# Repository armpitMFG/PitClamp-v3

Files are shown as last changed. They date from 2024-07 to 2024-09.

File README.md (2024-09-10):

# Note: This project is obsolete. Use [PitClamp Mini](https://github.com/armpitMFG/PitClamp-Mini) instead

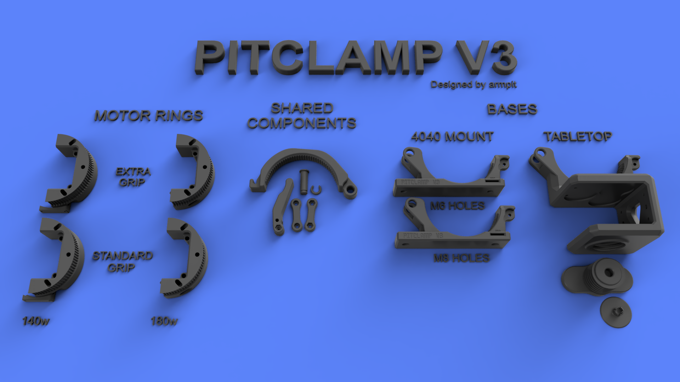
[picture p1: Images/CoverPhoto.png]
PitClamp v3 README Cover Photo


# PitClamp v3 Quick Release Nema23 Mount 
**Summary**  
Highly secure mounting and easy rotational adjustment of iHSV57 and 57AIM Nema23 motor  
Substantially stronger & grippier than previous PitClamp versions  
4 degree rotational granularity  
Supports sensor-homing cable passthrough  
Motor can be completely removed for storage  
Selection of bases for different use cases  

**Motor compatibility**  
- 180w JMC iHSV57 with v2 reference board  
  - Full 360 degree range of movement
- 140w JMC iHSV57 with v2 reference board
  - 80 degree (-40 to 40 from horizontal)
- 140w JMC iHSV57 with relocated (or future) reference board
  - Full 360 degree
- 100w JMC iHSV57 with v2 reference board
  - Not supported
- 100w JMC iHSV57 with relocated (or future) reference board
  - 200 degree (-100 to 100 from horizontal) 
- "Gold motor" 57AIM30C with relocated (or future) reference board
  - Full 360 degree

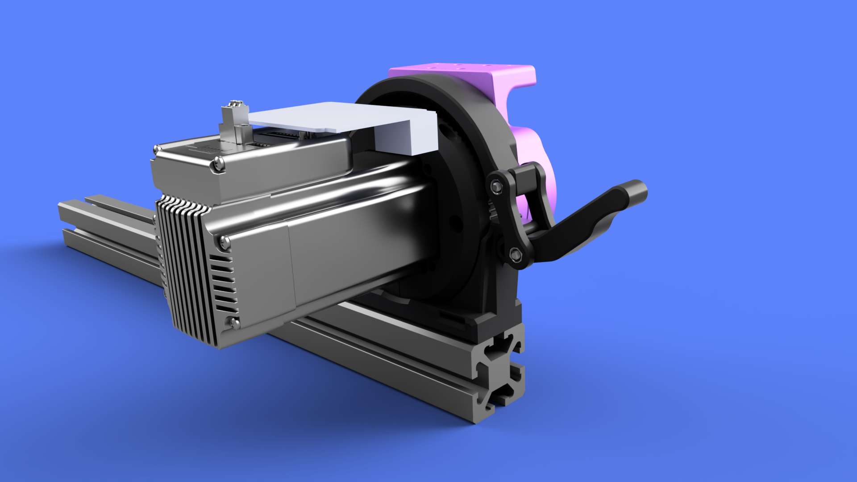
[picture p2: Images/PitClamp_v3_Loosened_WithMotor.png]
PitClamp v3 README Cover Photo2
  

## [PitClamp v3 - Motor Rings](Files/Motor%20Rings)
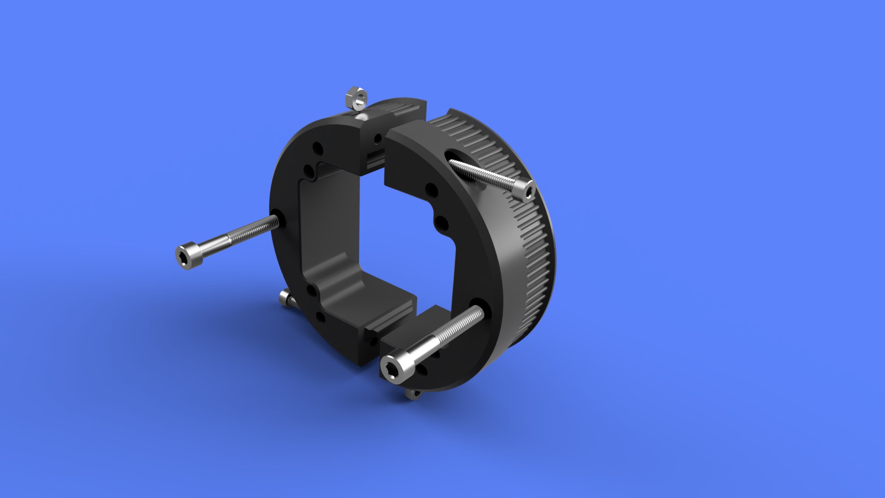
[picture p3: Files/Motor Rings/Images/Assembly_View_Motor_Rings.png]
Motor Rings Assembly View
  

**Summary**  
Motor rings for attaching iHSV57 and 57AIM Nema23 motors to PitClamp v3 mounts  

**File variations**  
- EXTRAGRIP
  - Clunkier adjustment, but provides extra grip strength
  - Not recommended unless you have grip issues with the standard
- 140w
  - Supports 140w motors with v2 reference board mounting support
  - Pair one of these with a standard half if you use 140w

**Part list**  
- Motor Ring Half
- Motor Ring Half EXTRAGRIP
- Motor Ring Half 140w
- Motor Ring Half EXTRAGRIP 140w

**Hardware**  
- 2x M4x16 (M4x25 max) Socket Cap Head Bolt (w/ Optional 2x M4 Nut for added strength, likely unnecessary)
- 2x M5x35 (M5x50 max) Socket Cap Head Bolt (To attach to OSSM body)

**Printing**  
3 walls 20% infill  
No supports necessary  
(Must print with 0.2mm layer height for built-in support assists to work)  
If using 180w motor rings, print your selected ring twice; If using 140, replace one ring with the corresponding 140w variant  

**Assembly**  
(Optional, likely unnecessary) Insert M4 nut into each motor half slot  
Slide ring halves over motor and connect using M4x16 (M4x25 max) Socket Cap Head Bolt  
Connect motor ring assembly to OSSM Base using 2x M5x35 Socket Cap Head Bolts  

## [PitClamp v3 - Shared Components](Files/Shared%20Components/)
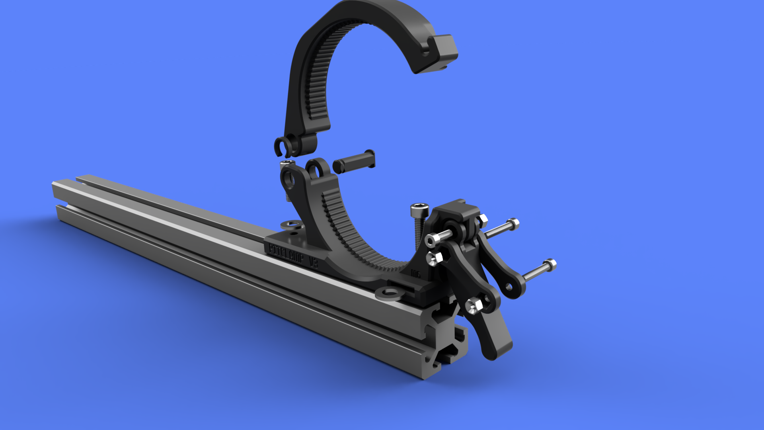
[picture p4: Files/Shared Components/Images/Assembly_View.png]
PitClamp v3 - Shared Components
  

**Summary**  
Components shared among all PitClamp v3 mounting bases

**Part list**
- Ring Upper
- Hinge Pin
- Hinge Pin Clip
- Handle
- Dogbone (Nut inset)
- Dogbone (Bolt inset)

**Hardware**  
- 2x M4x25 Socket Cap Head Bolt
- 1x M4x12 Socket Cap Head Bolt
- 3x M4 Nut

**Printing**  
3 walls 30% infill  
(Must print with 0.2mm layer height for built-in support assists to work)  
Supports required for Handle  

**Assembly**  
Insert M4 nuts into the Dogbone and Handle  
Attach Handle to the Ring Base using M4x12 Socket Cap Head Bolt (Hand tighten until snug, then back off 1/4 turn)  
Attach Dogbones to the Handle using M4x25 Socket Cap Head Bolt (Hand tighten until snug, then back off 1/4 turn)  

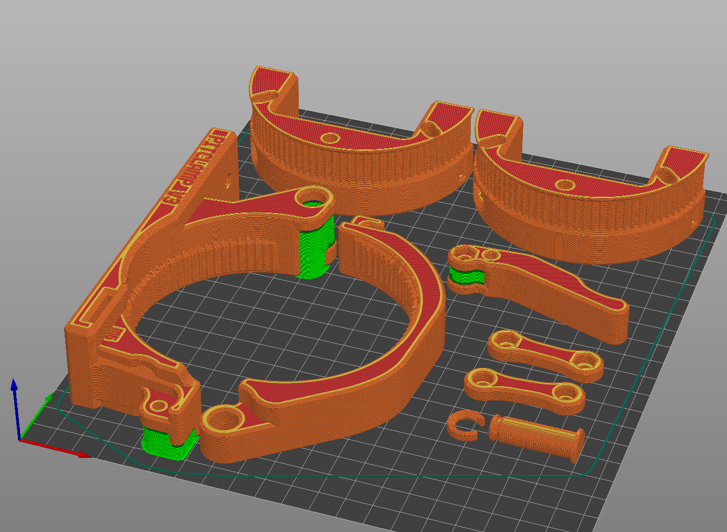
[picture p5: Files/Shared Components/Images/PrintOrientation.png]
PitClamp v3 - Shared Components
  

## [PitClamp v3 - 4040 Base](Files/Bases/40-4040)
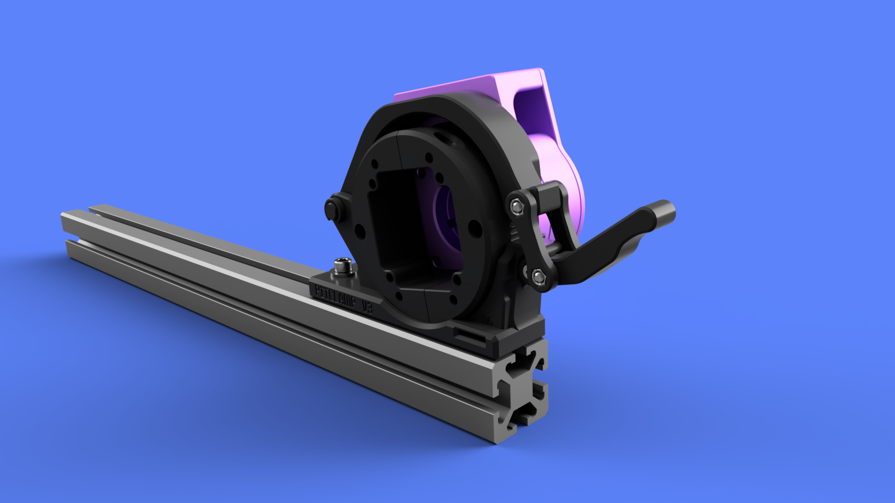
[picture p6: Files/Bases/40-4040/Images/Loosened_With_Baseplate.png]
PitClamp v3 - 4040 Base
  
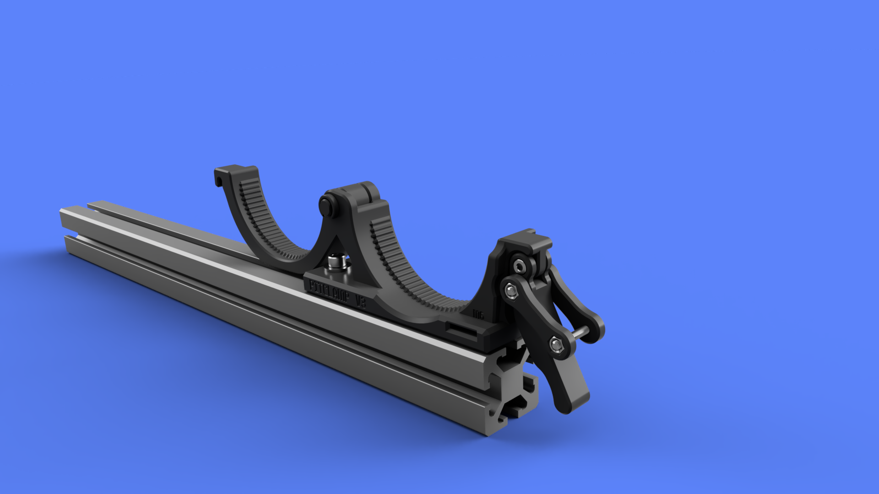
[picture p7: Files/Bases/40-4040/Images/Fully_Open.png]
PitClamp v3 - 4040 Base
  

**Summary**  
Base for attaching PitClamp v3 to 4040 aluminum extrusion  
60mm height when in 'storage' mode  

**File variations**  
- Ring Base M6 mounting hardware
- Ring Base M8 mounting hardware
  
**Hardware**  
- 2x M6x20 Socket Cap Head Bolt
- 2x ~12mm diameter M6 Washer (16mm max diameter, 2.4mm max thickness)
- 2x M6 T-Nut

**Printing**  
3 walls 30% infill  
(Must print with 0.2mm layer height for built-in support assists to work)  
Minimal supports around the hinge and handle attachment points  

**Assembly**  
Use M6x20 Socket Cap Head Bolt (or M8 on M8 version) and T-Nut to attach to 4040, washer for front slides into slot  
Attach Ring Upper to Ring Base using Hinge Pin and affix Hinge Pin Clip  

PitClamp v3 - 4040 Base Print Orientation  

## [PitClamp v3 - Tabletop Base](Files/Bases/Tabletop/)  

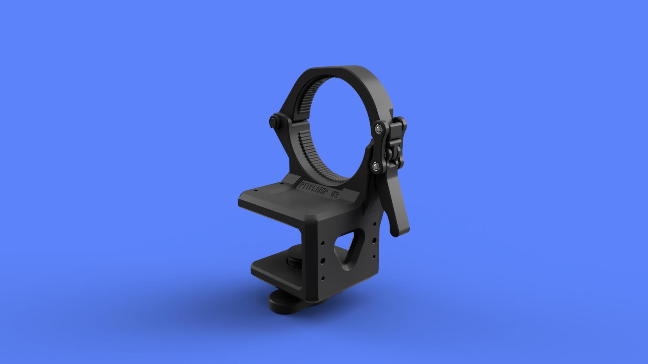
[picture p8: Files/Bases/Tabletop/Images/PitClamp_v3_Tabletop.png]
PitClamp v3 - Tabletop Base
  

**Summary**  
Allows for clamping to a tabletop, door or similar, ranging from 30mm-50mm  
For use with stroker attachments or for light-duty insertable use when attached to an interior door  

**Hardware**  
38mm furniture non-slip pads. Inexpensive, ~$3USD local or Amazon for 8pc.  
https://www.scotchbrand.com/3M/en_CA/p/d/v000277260/  

**Printing**  
3 walls, 30% infill minimum; More walls for stiffer clamp  
(Must print with 0.2mm layer height for built-in support assists to work)  
Minimal supports around the hinge and handle attachment points, but for cleaner threads you can use support there, too  
I chose not to support threads and worked fine on Ender3 v1 w/ PETG  
The screw and screw topper do not need support  

**Assembly**  
(Optional, but highly recommended) Attach 3 furniture gripping pads to the underside of the Tabletop Mount and 1 gripping pad to Screw Topper.  
Thread Screw through the Tabletop Mount and then snap Screw Topper into place

**Addons**  
M4,M6,M4 holes with 15mm spacing on center to support addons  
Currently no add-ons have been created  

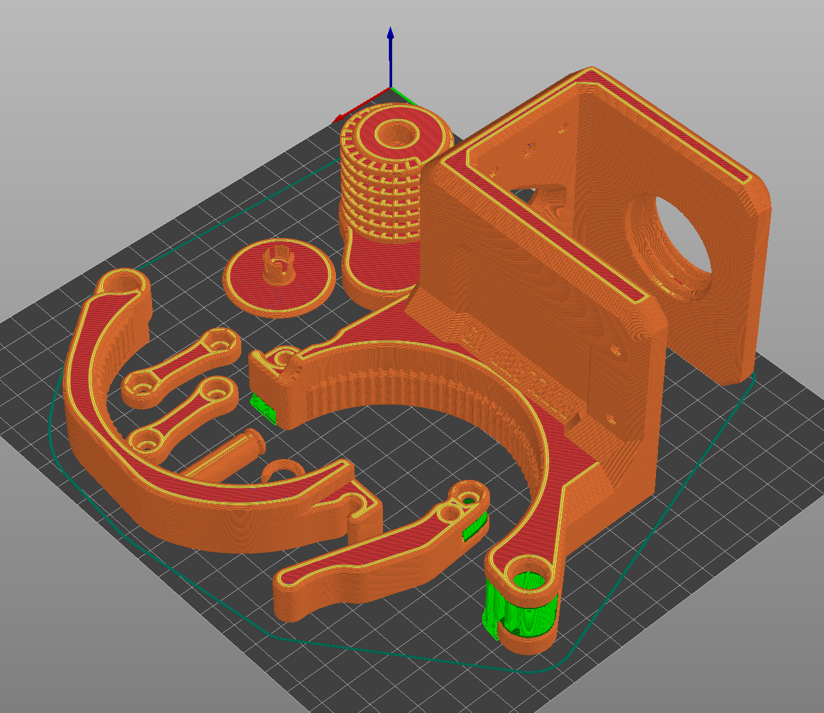
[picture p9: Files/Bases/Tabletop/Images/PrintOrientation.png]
PitClamp v3 - Tabletop Base Print Orientation


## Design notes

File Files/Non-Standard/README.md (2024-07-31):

These are non-standard parts that may be better for certain setups  

## Official non-standard parts:  
  
### /Handles/Handle_Forward
Remix author: armpit  
Default handle with an 80 degree bend to allow for PitClamp v3 use in setups where the handle cannot extend down past the PitClamp Base  

## 3rd party non-standard parts:  

### /20-4040/PitClamp_v3_Ring_Base_M5
Remix author: Macarize  
Default PitClamp v3 Base - 4040, but for 20-4040 extrusion and M5 holes  
  
### /dbiesn Head/PitClamp_v3_Motor_Ring_Half_EXTRAGRIP_dbiesn_head
Remix author: Jack   
Default Motor Ring Half EXTRAGRIP version for use with the dbiesn head

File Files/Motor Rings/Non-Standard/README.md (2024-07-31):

Same as normal ring, but the grooves are rotated 2 degrees which will point the device directly horizonal.

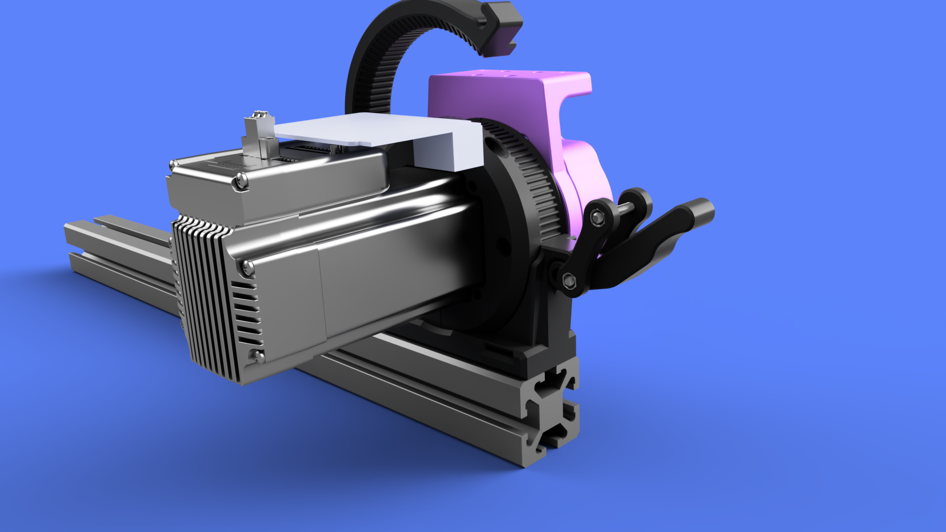
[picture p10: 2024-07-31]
Images/PitClamp_v3_Opened_WithMotor.png

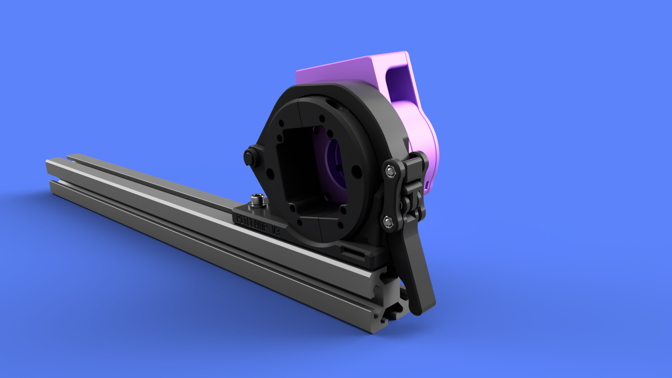
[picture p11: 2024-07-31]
Files/Bases/40-4040/Images/Clamped_With_Baseplate.png

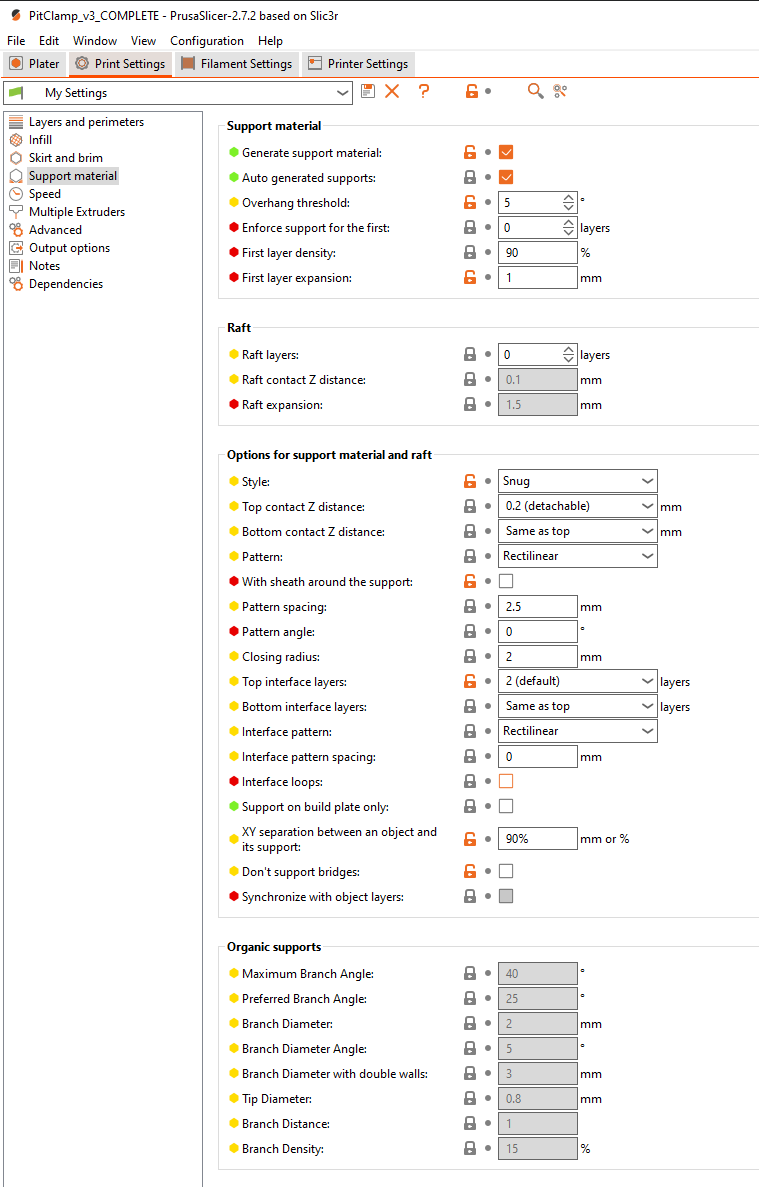
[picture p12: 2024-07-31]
Files/Bases/Tabletop/Images/SupportSettings.png

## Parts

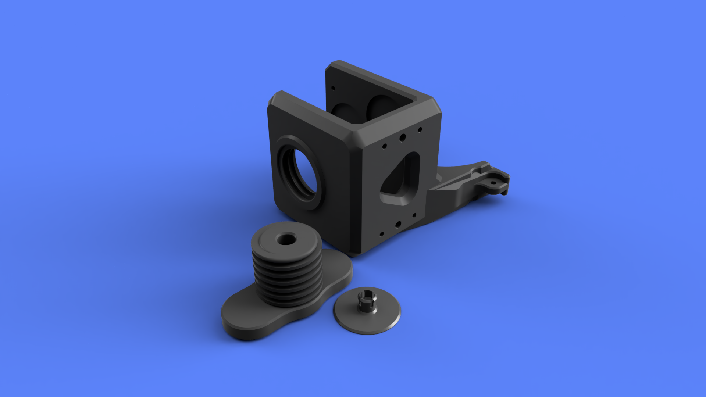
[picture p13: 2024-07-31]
Files/Bases/Tabletop/Images/PitClamp_v3_Tabletop_Parts.png

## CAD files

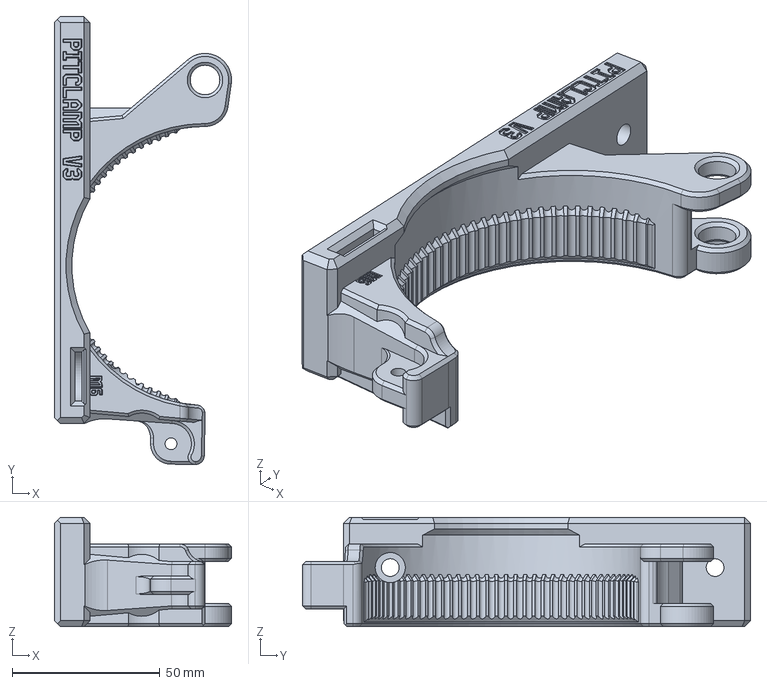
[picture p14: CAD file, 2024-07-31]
Files/Bases/40-4040/STEP/PitClamp_v3_Ring_Base_M6.step
60.0 x 151.7 x 37.0 mm

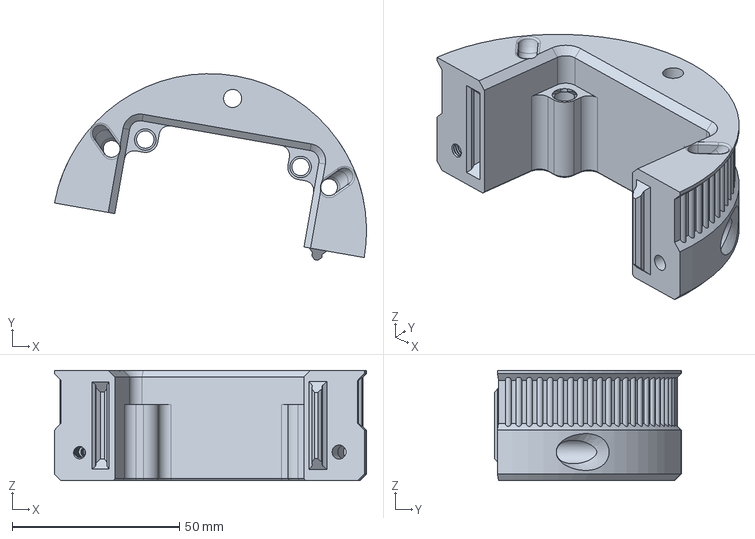
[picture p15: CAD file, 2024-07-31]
Files/Motor Rings/Non-Standard/PitClamp_v3_Motor_Ring_Half_HorizontalCompat.step
93.2 x 55.8 x 33.0 mm

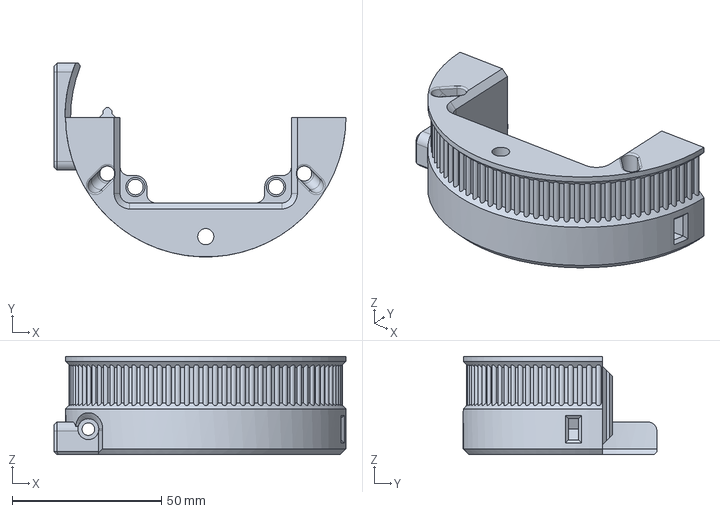
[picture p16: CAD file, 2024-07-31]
Files/Motor Rings/STEP/PitClamp_v3_Motor_Ring_Half_iHSV57-140w.step
97.9 x 64.9 x 33.0 mm

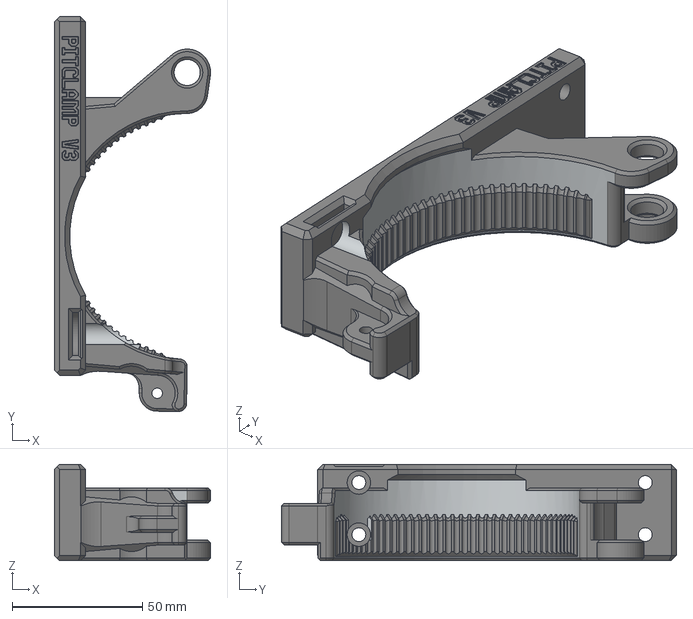
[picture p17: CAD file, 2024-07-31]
Files/Non-Standard/20-4040/STEP/PitClamp_v3_Ring_Base_M5.stp
60.0 x 151.7 x 37.0 mm

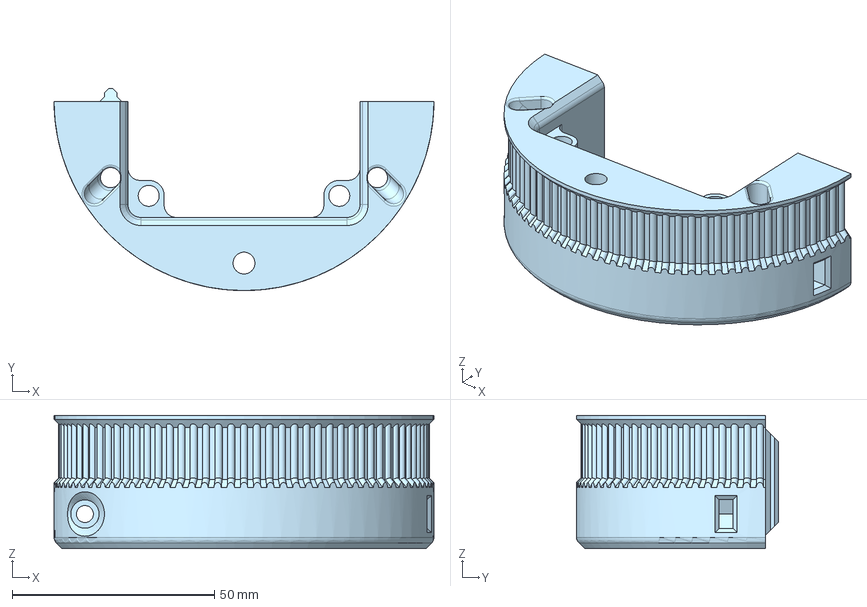
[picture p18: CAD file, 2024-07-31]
Files/Non-Standard/dbiesn Head/STEP/PitClamp_v3_Motor_Ring_Half_EXTRAGRIP_dbiesn_head.step
94.0 x 50.0 x 33.0 mm

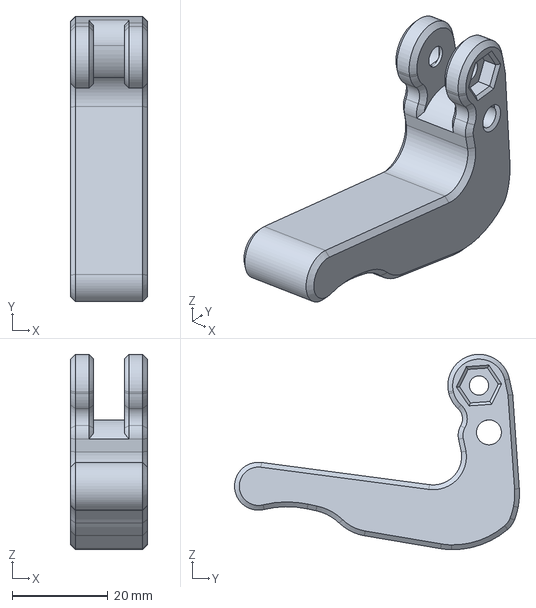
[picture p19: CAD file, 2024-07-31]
Files/Non-Standard/Handles/STEP/PitClamp_v3_Handle_Forward.step
16.0 x 59.5 x 40.8 mm

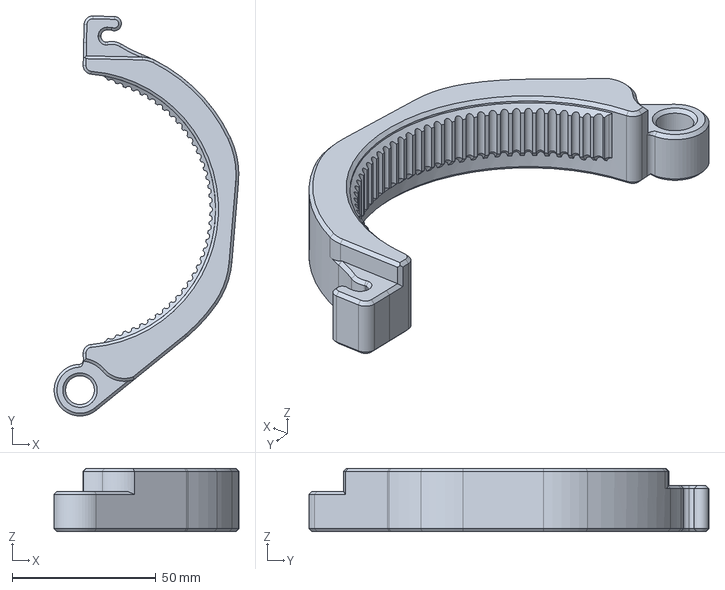
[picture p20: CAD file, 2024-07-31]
Files/Shared Components/STEP/PitClamp_v3_Ring_Upper.step
64.3 x 139.2 x 22.0 mm

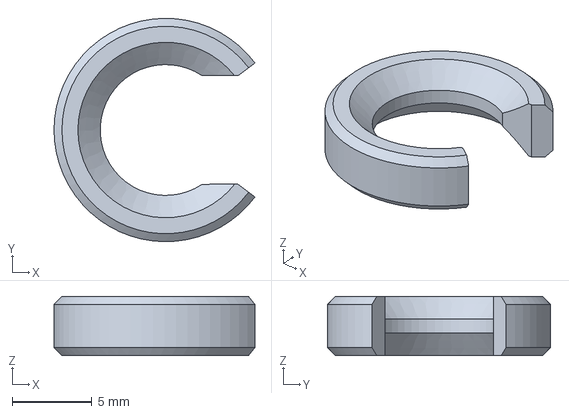
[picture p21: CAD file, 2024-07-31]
Files/Shared Components/STEP/PitClamp_v3_Hinge_Pin_Clip.step
12.6 x 14.0 x 3.70 mm

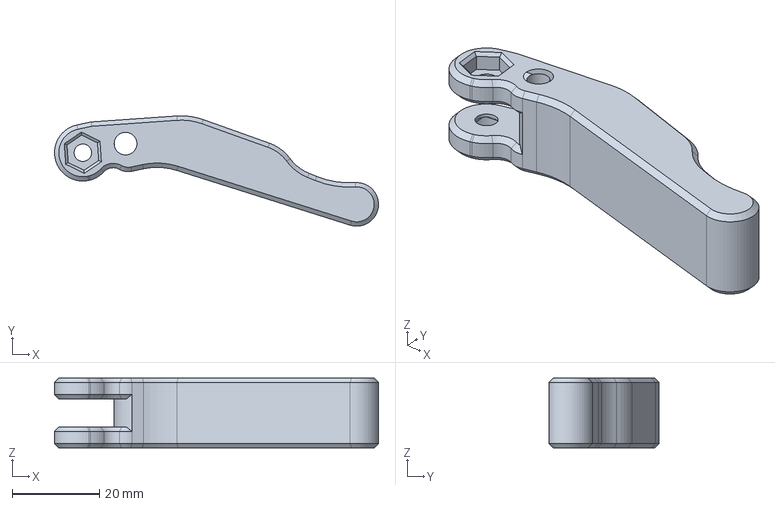
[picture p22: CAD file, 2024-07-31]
Files/Shared Components/STEP/PitClamp_v3_Handle.step
74.2 x 25.3 x 16.0 mm

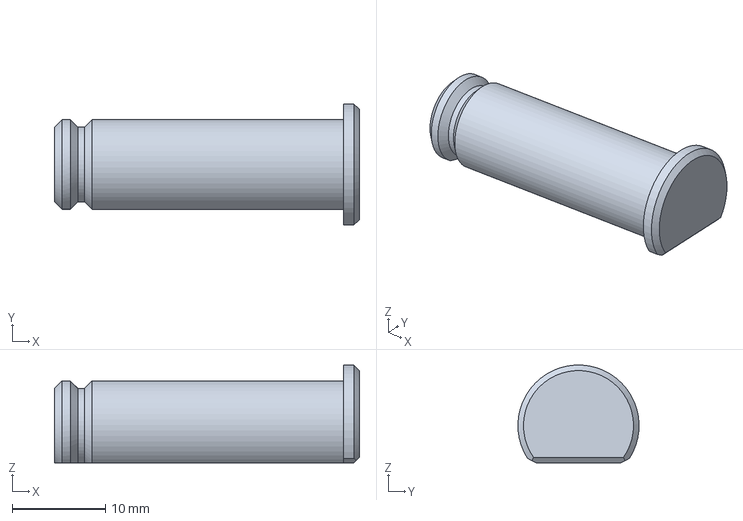
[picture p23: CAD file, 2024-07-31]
Files/Shared Components/STEP/PitClamp_v3_Hinge_Pin.step
32.7 x 13.0 x 10.5 mm

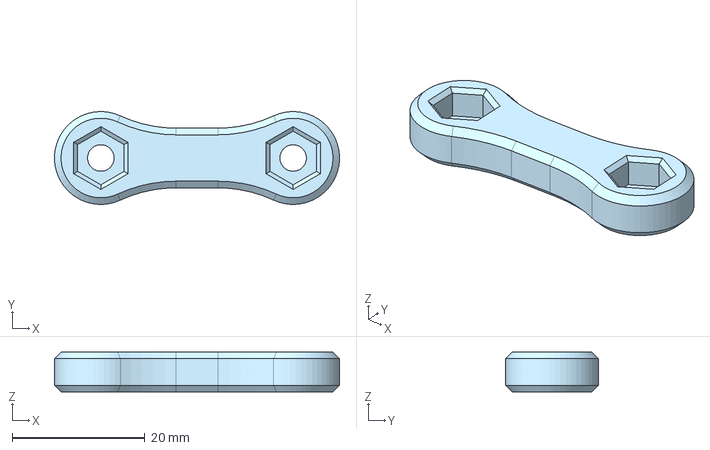
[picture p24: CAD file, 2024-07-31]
Files/Shared Components/STEP/PitClamp_v3_Dogbone_Nuts.step
43.0 x 14.0 x 6.00 mm

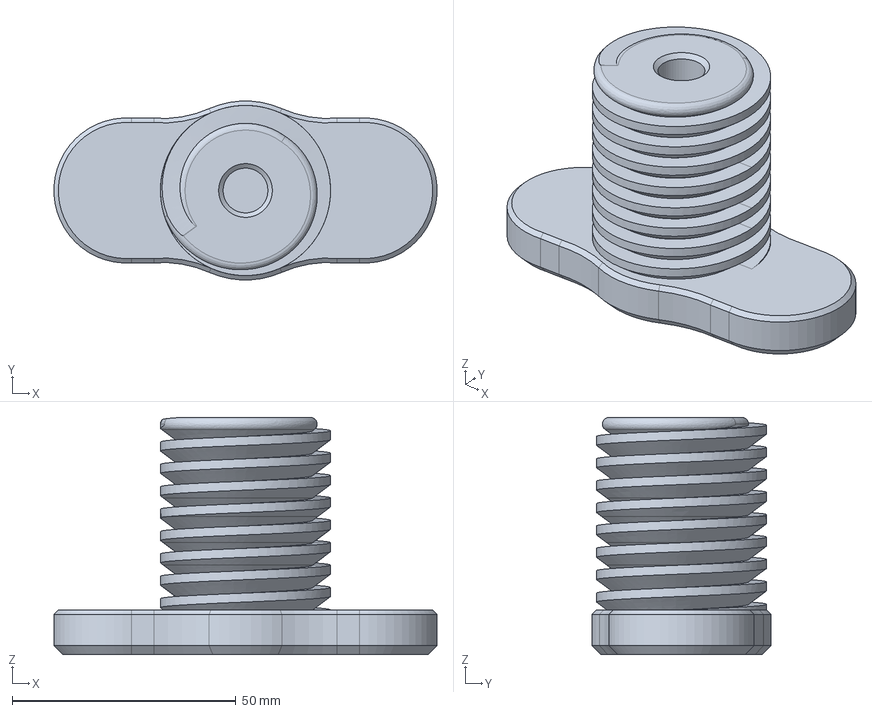
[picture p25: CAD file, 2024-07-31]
Files/Bases/Tabletop/STEP/PitClamp_v3_Tabletop_Screw+10mm.step
85.5 x 39.9 x 53.0 mm

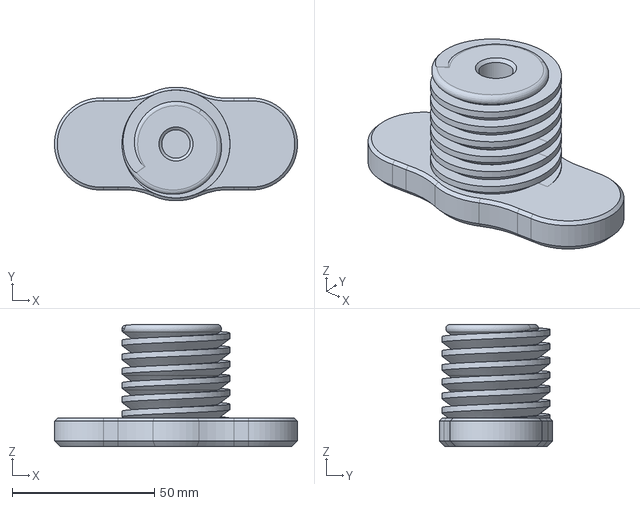
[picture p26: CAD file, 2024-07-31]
Files/Bases/Tabletop/STEP/PitClamp_v3_Tabletop_Screw.step
85.5 x 39.9 x 43.0 mm

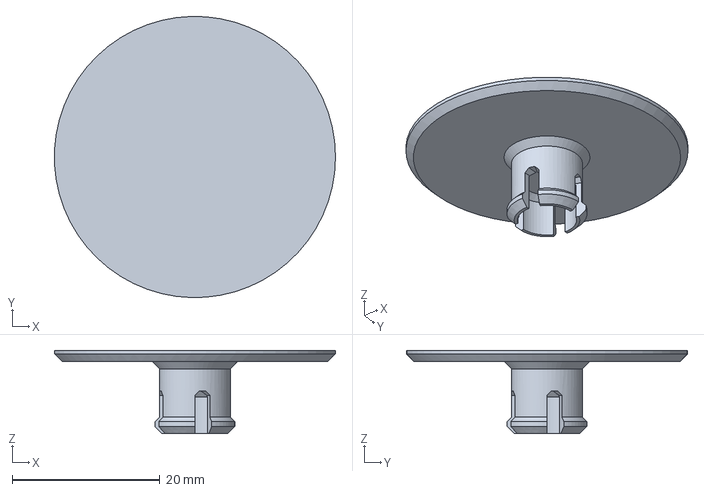
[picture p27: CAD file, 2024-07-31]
Files/Bases/Tabletop/STEP/PitClamp_v3_Tabletop_Screw_Topper.step
38.1 x 38.1 x 11.3 mm

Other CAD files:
Files/Bases/40-4040/Non-Standard/STEP/PitClamp_v3_Ring_Base_M8.step
Files/Motor Rings/STEP/PitClamp_v3_Motor_Ring_Half.step
Files/Shared Components/STEP/PitClamp_v3_Dogbone_Bolts.step
Files/Bases/40-4040/Non-Standard/PitClamp_v3_Ring_Base_M8.stl
Files/Bases/40-4040/PitClamp_v3_Ring_Base_M6.stl
Files/Bases/Tabletop/PitClamp_v3_Tabletop_Screw+10mm.stl
Files/Bases/Tabletop/PitClamp_v3_Tabletop_Screw.stl
Files/Bases/Tabletop/PitClamp_v3_Tabletop_Screw_Topper.stl
Files/Motor Rings/Non-Standard/PitClamp_v3_Motor_Ring_Half_HorizontalCompat.stl
Files/Motor Rings/PitClamp_v3_Motor_Ring_Half.stl
Files/Motor Rings/PitClamp_v3_Motor_Ring_Half_iHSV57-140w.stl
Files/Non-Standard/20-4040/PitClamp_v3_Ring_Base_M5.stl
Files/Non-Standard/Handles/PitClamp_v3_Handle_Forward.stl
Files/Non-Standard/dbiesn Head/PitClamp_v3_Motor_Ring_Half_EXTRAGRIP_dbiesn_head.stl
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

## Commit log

2024-07-31 Initial commit - Refactor beta into release repo
    [PitClamp_v3_Dogbone_Bolts.step, PitClamp_v3_Dogbone_Bolts.stl, PitClamp_v3_Dogbone_Nuts.step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]
2024-07-31 Add +10mm length screw for Tabletop Base
    [PitClamp_v3_Tabletop_Screw+10mm.step, PitClamp_v3_Tabletop_Screw+10mm.stl]
2024-07-31 Add HorizontalCompat ring
    [PitClamp_v3_Motor_Ring_Half_HorizontalCompat.step, PitClamp_v3_Motor_Ring_Half_HorizontalCompat.stl]
2024-08-03 Fix scaling issue
    [PitClamp_v3_Dogbone_Nuts.stl]
